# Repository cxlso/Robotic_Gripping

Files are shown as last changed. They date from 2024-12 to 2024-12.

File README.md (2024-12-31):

# Robotic Gripping
###### An example of a custom pneumatic gripper integration to get started with pneumatic actuation on a robotic arm.

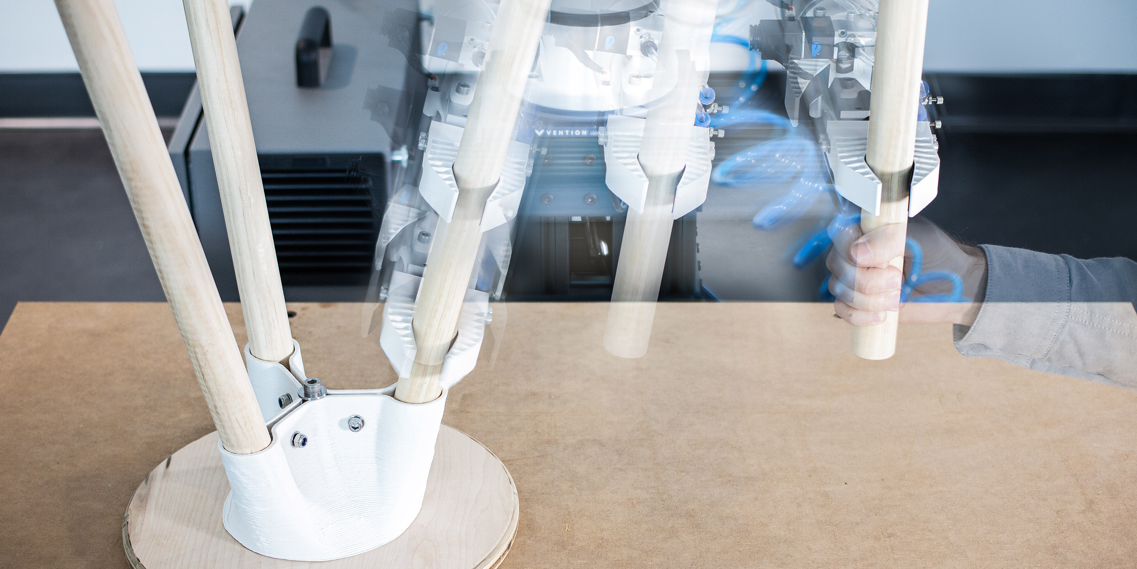
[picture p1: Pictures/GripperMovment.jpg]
GripperMovement


## Overview
This repository contains everyting needed to get an understanding on how to integrate a pneumatic actuator on a robotic arm, in our case the [Universal Robot UR10e](https://www.universal-robots.com/products/ur10-robot/) (or any UR model) through the example of a bespoke and affordable pneumatic gripper system.

Included in the repository are:

- Custom Pneumatic Gripper CAD Files: For 3D printing the mountable structure of the gripper and the flexible fingers,
- Wiring Diagram: Including both pneumatic an electrical wiring information,
- Scripts: Grasshopper toolpath example.

## Note on the Signal Workflow

The workflow begins with the Grasshopper script embedding the extrusion commands (open and closed) into the URP file. This file instructs the UR10e to output a digital voltage signal (0-24V) on the digital ouput 0 of the tool I/O M8 female port (TO0). These signals is directly interpreted by the electronic solenoid valve to balance the airflow between output A (open) and B (closed), ultimately actuating the MHC2-25D pneumatic gripper.

The digital signals can also be overwritten in real-time using the UR Teaching Pendant as demonstrated in the first video.

**Grasshopper (Extrusion Command Embeded in URP file/G-Code ) ⟶ UR10e (Digital Output 0-24V) ⟶ Electronic Solenoid Valve (Gate A-B) ⟶ MHC2-25D Pneumatic Gripper (Open-Closed)**

## Components

- Generic MHC2-25D Pneumatic Gripper
- Generic 5-way 2-position Electronic Solenoid Valve (4V210-08)
- 6mm Pneumatic Pipe Kit 
- M5 6mm 90deg Pipe Fittings
- M5 and M6 Hex Socket Head Screws (Mostly short)
- Electrical Connectors (JST XH in our case)
- M8 8 Pin Female Connector Cable

Both pneumatic gripper and electronic solenoid valve are industrial-grade, affordable, and readily available.
This whole setup cost less than 60 USD at the time of writing.

## Setup and Installation

### Prerequisites

- UR10e Robotic Arm (or any UR models),
- Afformentioned Components,
- Air Compressor,
- Rhino Grasshopper: For generating toolpath commands.

### Wiring Diagram

Refer to the following wiring diagram for the electrical connections.

Wiring_Diagram
Diagram made with the open-source tool [Fritzing](https://fritzing.org/).

### CAD Files

A structural body system fitting the robotic arm's flange was designed and fabricated connecting a generic MHC2-25D pneumatic gripper and a generic 5-way, 2-position solenoid valve. Based on [the fin ray effect](https://doi.org/10.1007/s40430-024-04957-0), an adaptative and interchageable set of robotic fingers was also modeled.
The later were also 3D printed with PLA and are working as expected. However, a PETG or TPU version would yield better results although the design would need to be adapted.

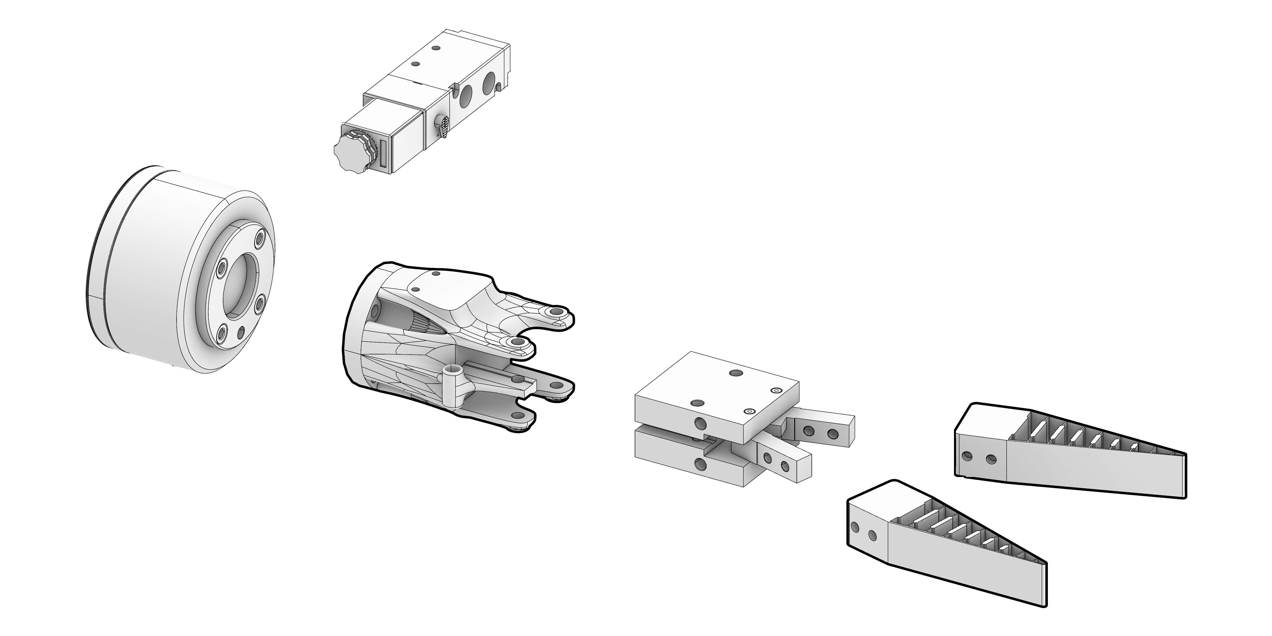
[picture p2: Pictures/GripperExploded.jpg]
GripperExploded


- [Gripper_Body](CAD/Gripper_Body.stl) 3D printing file.
- [Adaptative_Fingers](CAD/Adaptative_Fingers.stl) 3D printing file.

If customization is desired, a [Rhino file](CAD/Pneumatic_Gripper_System.3dm) of the gripper system is in the repository.

### Grasshopper Definition

To control the pneumatic gripper on the UR10e, a basic Grasshopper definiton was made: 

**[RoboticGripping_Basic_Script](Script/RoboticGripping_Basic_Script.gh)**

This definition is based on a previous work about [Robotic Printing](https://github.com/cxlso/Robotic_Printing), follows the same visual framework and is also using the [Robots](https://www.food4rhino.com/en/app/robots) plugin by Visose.

Instead of using the standard "Set Digital Output" component from the Robots plugin, the "Custom Command" was used to manualy set the tool digital output with the following commands: "set_tool_digital_out(0, True)" and "set_tool_digital_out(0, False)". 

This work-around was required because TO0 or TO1, the digital outputs of the flange can't be accessed with the standrad "Set Digital Output" (DO). The solution was found in this [discussion](https://github.com/visose/Robots/discussions/222).

RoboticGripping_Basic_Script

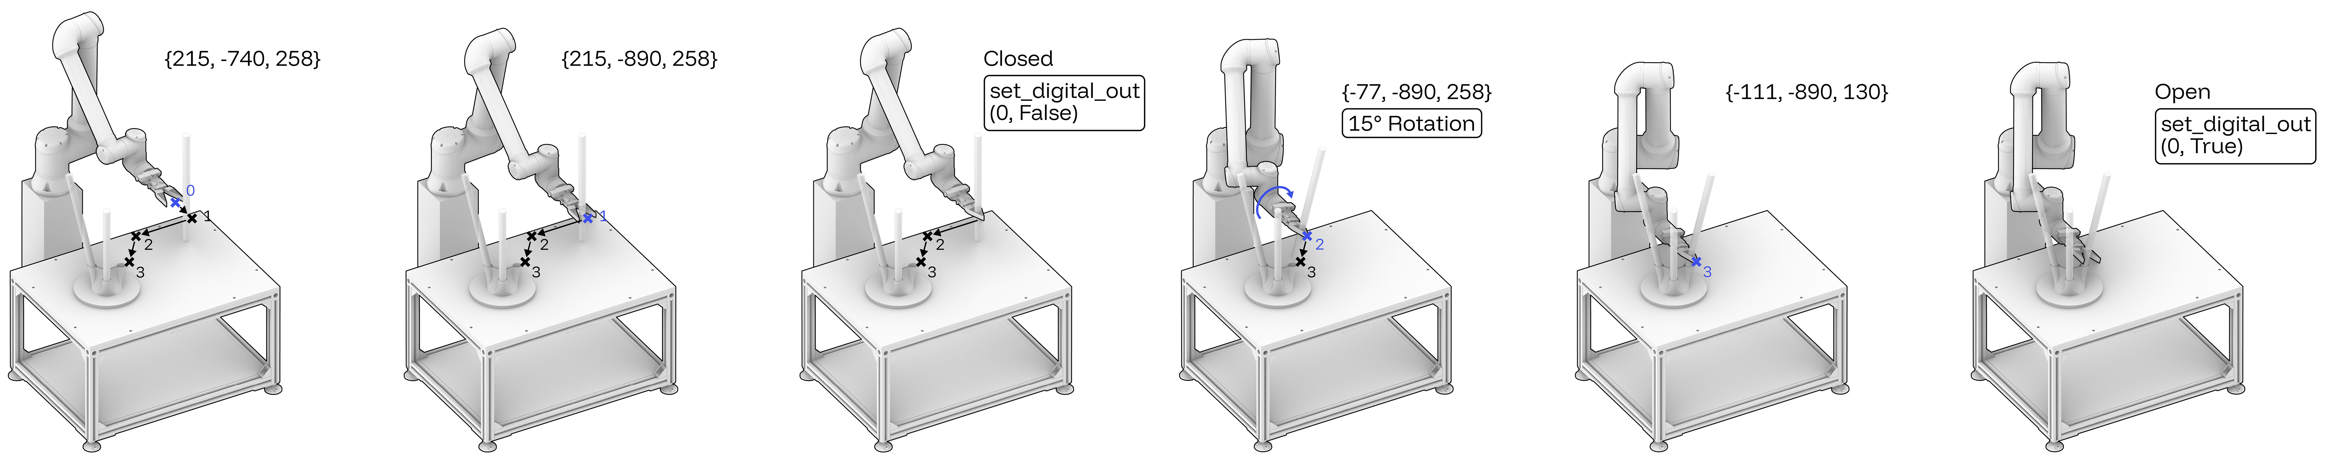
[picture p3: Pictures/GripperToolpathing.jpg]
GripperToolpathing


## Pictures and Videos

https://github.com/user-attachments/assets/d02727e6-7be6-4e2c-b9e1-815e54aebf75

https://github.com/user-attachments/assets/525a650b-c3f4-41bc-b1ef-6184d4fb3f9b

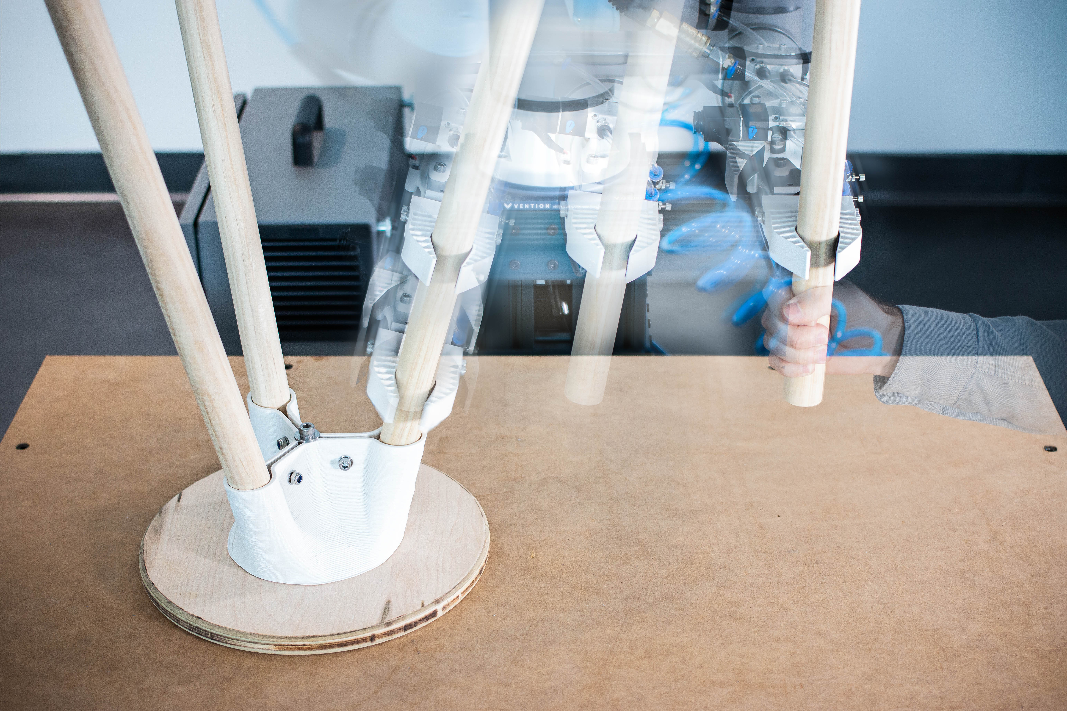
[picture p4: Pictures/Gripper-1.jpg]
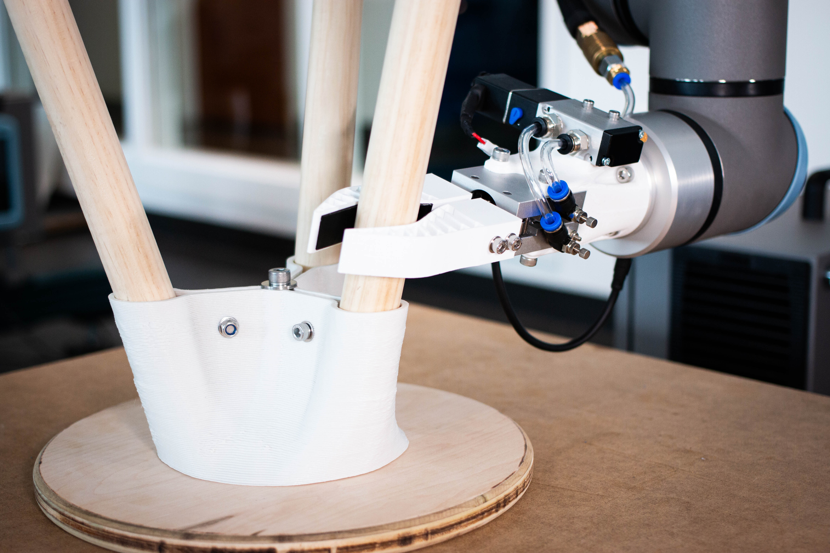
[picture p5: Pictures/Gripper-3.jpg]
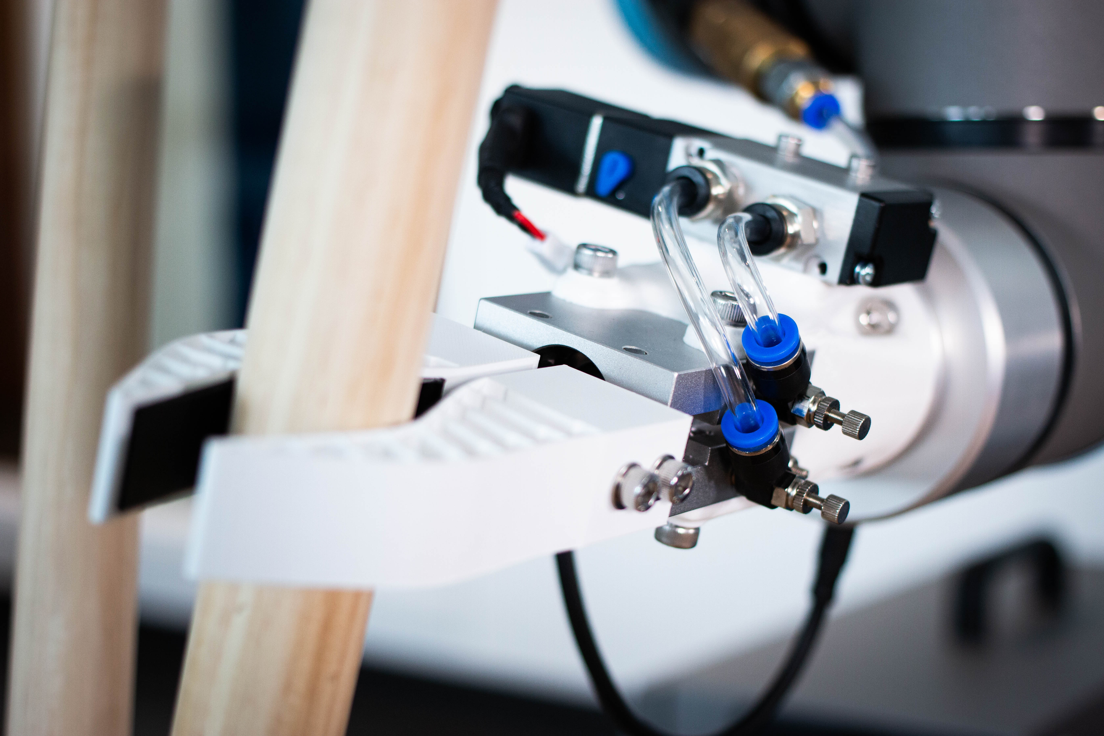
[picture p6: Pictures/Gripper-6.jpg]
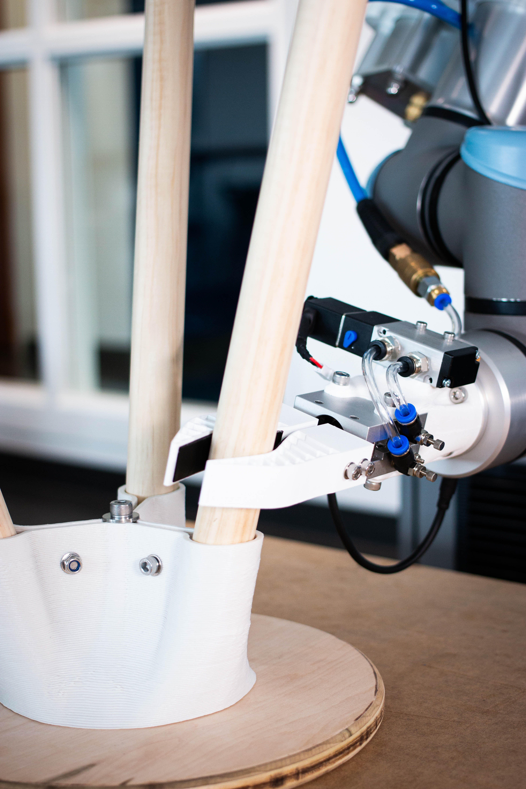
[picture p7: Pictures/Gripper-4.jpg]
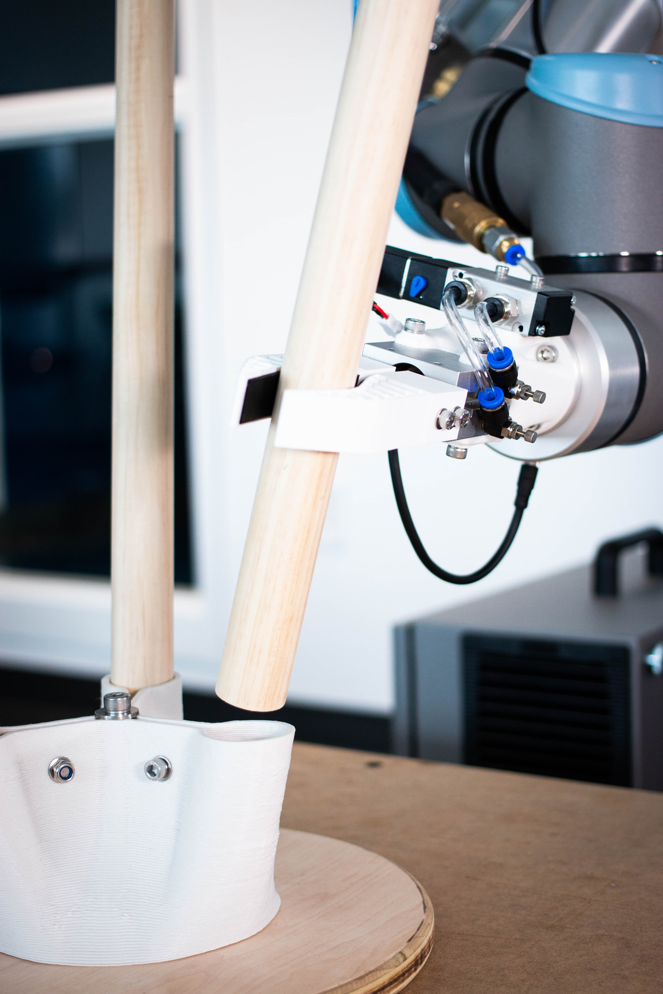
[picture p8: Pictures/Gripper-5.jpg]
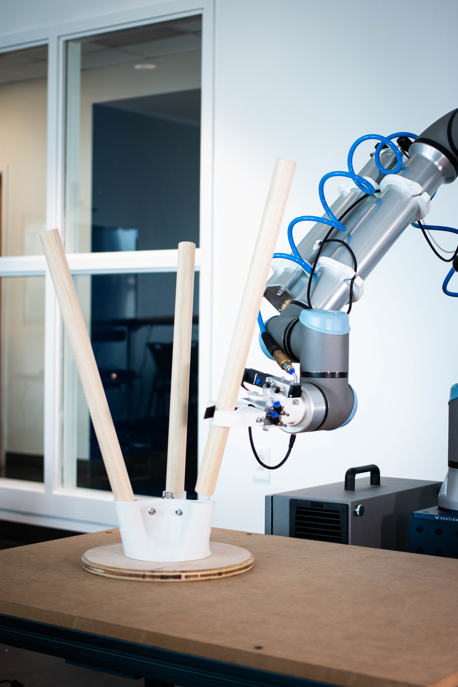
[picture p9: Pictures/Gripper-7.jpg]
      

## Contributing

Contributions are welcome! Please submit a pull request or open an issue to discuss any changes or improvements.

## License

[][cc-by-nc-sa]

This work is licensed under a
[Creative Commons Attribution-NonCommercial-ShareAlike 4.0 International License][cc-by-nc-sa].

[][cc-by-nc-sa]

[cc-by-nc-sa]: http://creativecommons.org/licenses/by-nc-sa/4.0/
[cc-by-nc-sa-image]: https://licensebuttons.net/l/by-nc-sa/4.0/88x31.png
[cc-by-nc-sa-shield]: https://img.shields.io/badge/License-CC%20BY--NC--SA%204.0-lightgrey.svg

## Acknowledgements

This project was developed on my own initiative at the [School of Architecture of Florida Atlantic University](https://www.fau.edu/artsandletters/architecture/) within the Environmental Design and Natural Materials lab, directed by Shermeen Yousif.

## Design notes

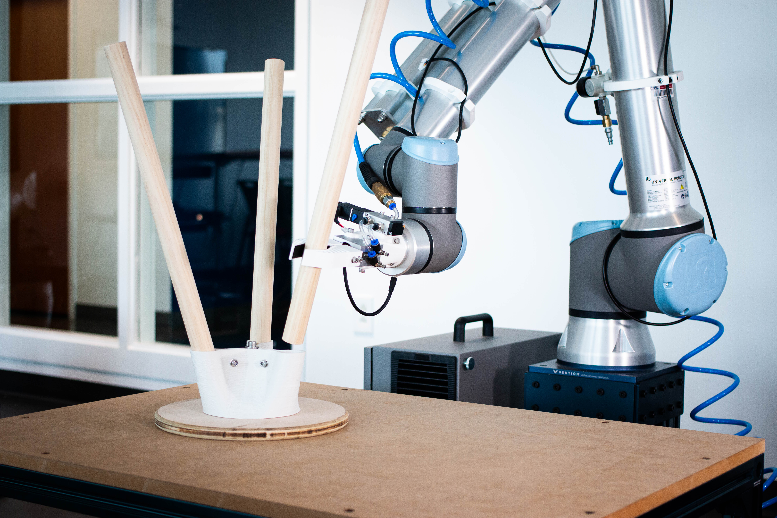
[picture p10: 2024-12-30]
Pictures/Gripper-8.jpg

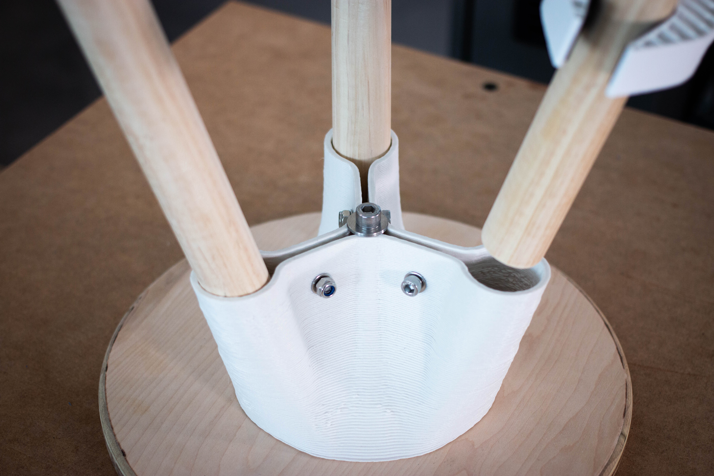
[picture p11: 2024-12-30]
Pictures/Gripper-9.jpg

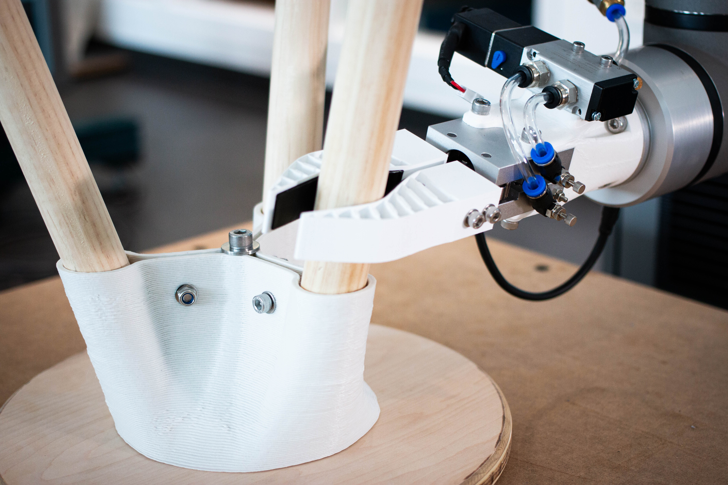
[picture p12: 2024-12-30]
Pictures/Gripper-2.jpg

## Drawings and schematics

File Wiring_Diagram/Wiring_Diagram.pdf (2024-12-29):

# Gripper End Effector

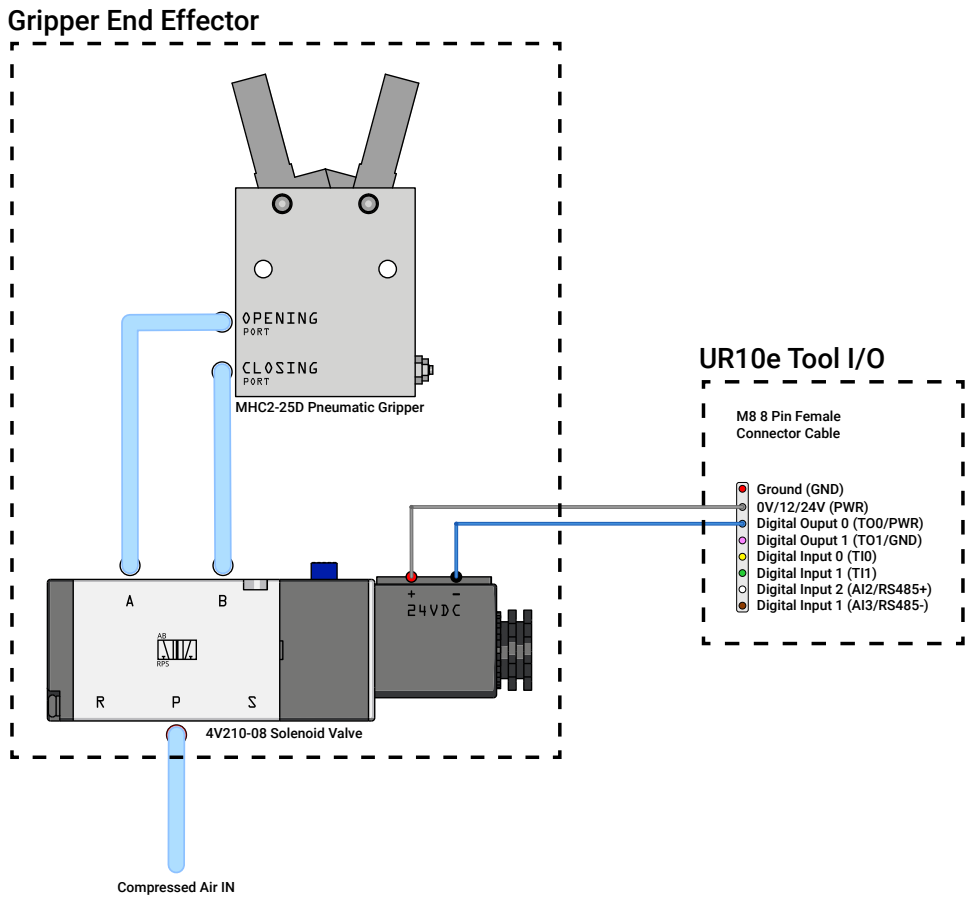
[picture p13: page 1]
M8 8 Pin Female Connector Cable; MHC2-25D Pneumatic Gripper; 4V210-08 Solenoid Valve; UR10e Tool I/O

Ground (GND)
0V/12/24V (PWR)
Digital Ouput 0 (TO0/PWR)
Digital Ouput 1 (TO1/GND)
Digital Input 0 (TI0)
Digital Input 1 (TI1)
Digital Input 2 (AI2/RS485+)
Digital Input 1 (AI3/RS485-)

Compressed Air IN

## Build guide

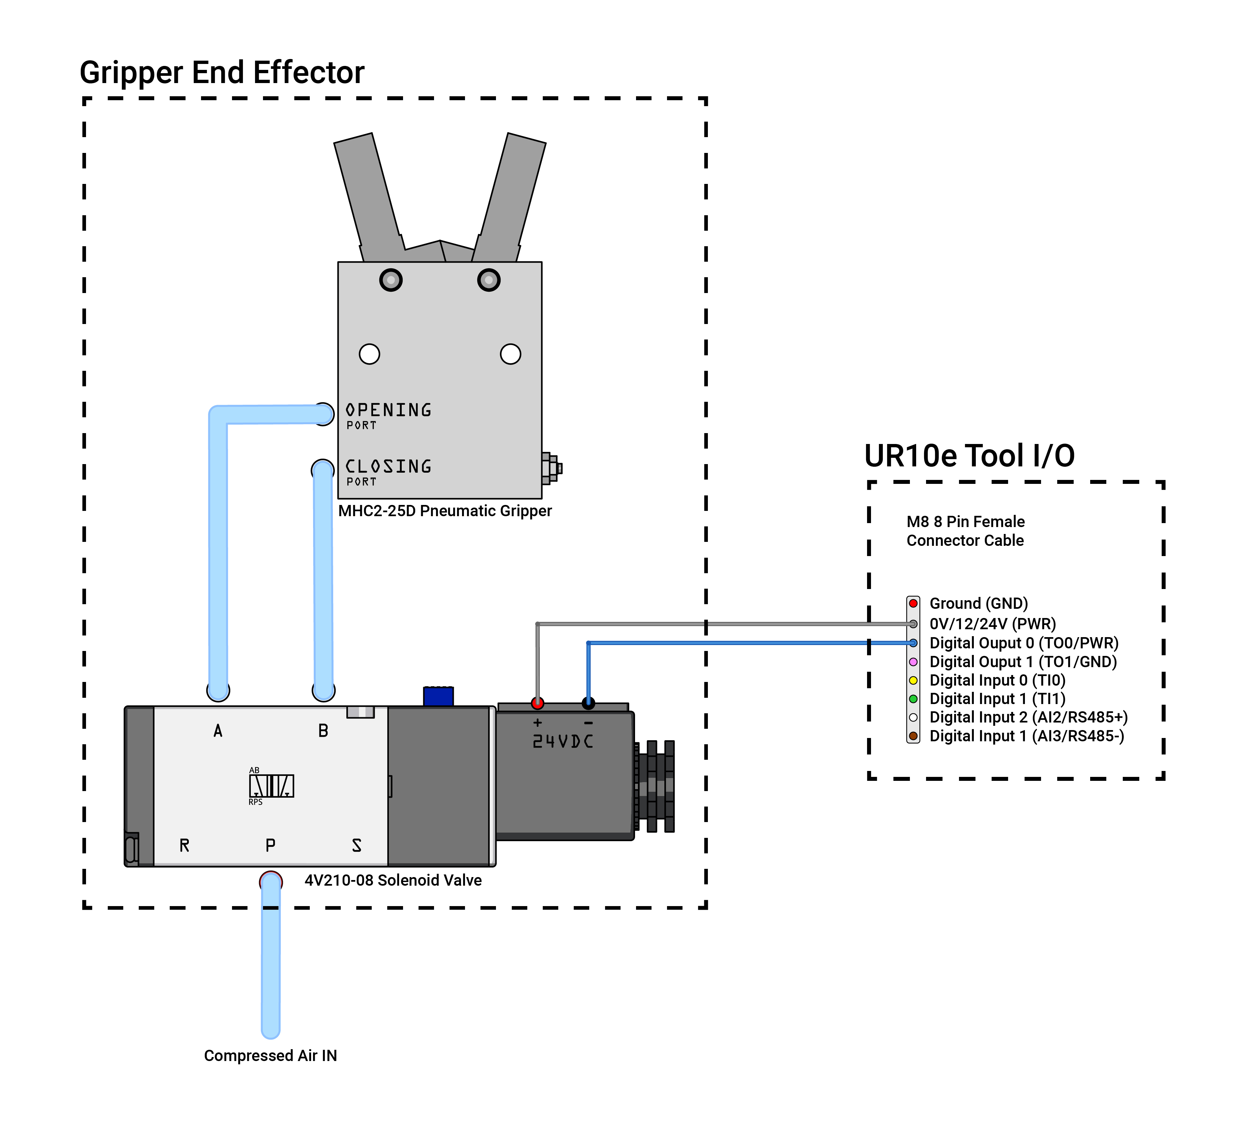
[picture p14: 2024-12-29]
Wiring_Diagram/Wiring_Diagram.jpg
